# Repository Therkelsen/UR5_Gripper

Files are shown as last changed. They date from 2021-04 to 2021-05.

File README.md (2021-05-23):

# UR5_Gripper
dRobTek Group 6 - Second semester project for B.E. in Robotics Technology
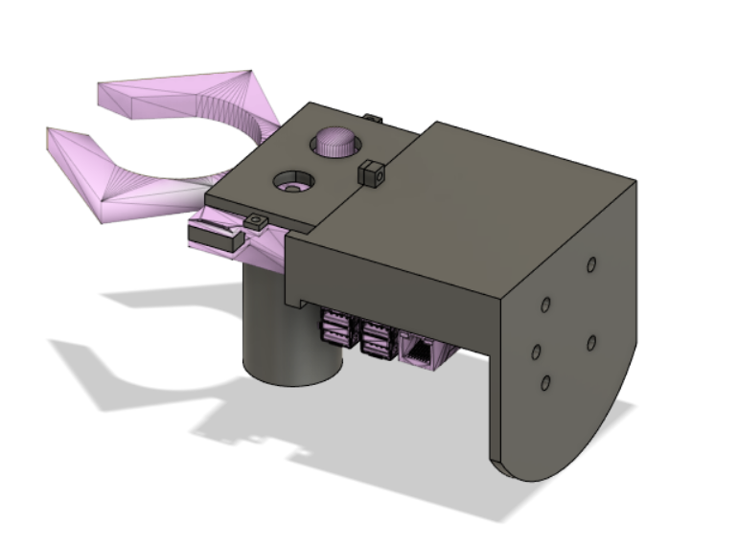
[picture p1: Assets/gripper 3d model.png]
UR5

<br>

## Problem
<div style="text-align: justify">A gripper for the Universal Robots UR5 robot is to be developed during this semester project. An idea could be to follow the block diagram below, but not required.</div>
<br>
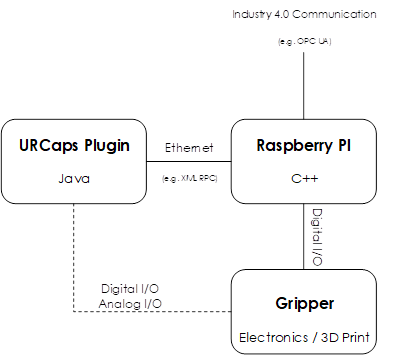
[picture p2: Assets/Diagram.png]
Diagram

<div style="text-align: justify">It is expected that you at least develop:<br>
•	A 3D model of a gripper that can be printed or otherwise constructed.<br>
•	Electronics to control the gripper.<br>
•	A URCaps plugin for the UR controller.<br>
•	Software design of a C++ Program developed on a Raspberry PI, a PC, or possibly both.<br>
•	A modern communication interface to the gripper (e.g. OPC UA). Ideas to an interface:<br>
•	The no. of grips<br>
•	Gripper force<br>
•	Gripper distance<br>
•	Etc.<br>
<br>
The gripper must fulfil the following requirements:<br>
•	Supply voltage: 24V (from external supply – you are not allowed to use the robot controller as power supply)<br>
•	The maximum gripper power use: 600mA<br>
•	It is not allowed to use the digital I/O from the UR robot. All I/O must be done through the Raspberry Pi microcontroller. Please remember that the power output from digital I/O is very limited.<br>
</div>
<br>

## Abstract
<div style="text-align: justify">
<a href="https://github.com/Therkelsen/UR5_Gripper/blob/main/Assets/Report.pdf">This report</a> presents the process of constructing and programming a gripper for the UR5-series industrial robotic arm, controlled through an XML-RPC-socket utilizing a URCap plugin on the robot. The gripper design is made for the purpose of hoisting a conventional 33 cl beverage can, which has the dimensions 122 mm in height and 65 mm in diameter. The final product is to be constructed with four main segments, firstly a URCap-plugin utilizing XML-RCP protocol to communicate with a Raspberry Pi. This single-board computer is connected to a motor, mounted to a 3D-printed gripper, which will open and close according to the XML-RPC-server method called by the URCap. Determinately, Industry 4.0 communication will run from the single-board computer to an external device, amassing and preserving information about the behaviour of the gripper.
<br>
First, the report introduces the different contents of the URCap-StarterPackage and the theoretical fundamentals of URCaps, following a walkthrough of the methods applied in building a URCap. This includes both an installation and program node fitting the criteria of the project. A more concrete view on how the individual Java-methods act together, to construct the interface and computer logics required in building a connection to an external device utilizing XML-RPC-protocol, is discussed. Furthermore, the structure of the C++-programmed XML-RPC-server will be covered, and additionally, how the different server method calls are utilized in another C++ program to instigate physical kineticism of the gripper. Thereafter, the designations and functionalities of the hardware components used will be listed and the process of modeling and printing the gripper, and the thoughts behind this design will be provided.
<br>
The proposed solution is presented in detail and discussed in terms of functionality in relation to the chosen scenario, and possible amendments, as well as thoughts on choices made throughout the process of effectuating a solution, will be shared. Lastly, the entire project will culminate in a summarized conclusion on the coalescence of URCaps, MotorControl, Industry 4.0 communication, and the 3D modeling and printing of the physical gripper - the four main segments embodying the objective of this project.
</div> 
<br>

## Introduction
<div style="text-align: justify">
The fourth industrial revolution as many in our time choose to call it, is constantly evolving, and evidently more of the industries as well as everyday processes, get automated. One of the many benefits of automation is, that the mistakes that humans make in the manual process are eliminated.
<br>
With this in mind, robots today are designed and constructed for all sorts of different purposes and in particular the 6-member robot arm has become an indispensable industrial tool, for example due to its universality.
This is not only due to the freedom of movement, but - as is the case for most robot arm manufacturers - also the freedom to switch between the robot arm tools. There are already a sea of tool manufacturers who invent everything between two- and three-finger grippers, vacuum grippers and grippers that utilize the so-called "soft robotics" technology. All these types of grippers, which can be used, for example, together with the robot arms from Universal Robots, which with their URCap software largely achieve the ambition of creating a universal robot arm.
<br>
The possibility of custom configuration through URCap allows for this project, where we have been given the task of designing and developing a gripper for a UR5 robot arm. This must be able to lift one or more objects of your choice. Here we have chosen to design a gripper that aims to lift a can, more specifically a standard 33 cl soda / beer can. The gripper itself is modeled in the CAD program Fusion 360, and is then physically made of 3D-printed plastic. The movements of the gripper are controlled by a DC motor, which is connected to a Raspberry Pi on which a motor driver is programmed using C++, to control the movement of the DC motor.
<br>
Furthermore, a URCap plugin has been developed in order to create a user-friendly interface. This URCap, consisting of a so-called Program Node and an Installation Node, establishes an XML-RPC connection to a server on the Raspberry Pi, thereby controlling the activation of the gripper's various functions.
</div>
<br>

## Conclusion
<div style="text-align: justify">
Through the work on the project, we have developed a well-functioning gripper in Fusion 360, with room in the gripper's cabinet for its electric components, for example the Raspberry Pi. 
<br>
The gripper is designed as consisting of two "fingers", designed to be able to carry an empty 33 cl soda / beer can. To control the gripper, a URCap, consisting of an installation and program node, has first been developed through Universal Robot's "URCap starter package". The installation node provides a UI for entering the port number and IP address, which is used to establish the XML-RPC connection. Through the program node, a UI has been programmed with a button for "grip" and "release", which call a method that makes an XML-RPC call to a C++ server that we have running on our Raspberry Pi. When this data is received, the C++ code executes the relevant method from the MotorControl class, depending on whether the URCap calls for a "grip" or "release", and here the gripper will do the physical action it is requested. 
<br>
We have tested the grip-release sequence and were able to successfully pick up a can and place it elsewhere. In addition, a TCP / IP connection has been created with the intention of Industry 4.0. Here, a comma-separated string is sent from the server, which tells the number of grips and the gripper's current state. Here, through a UI, the client side can monitor this data from an external device. Based on the problem formulation, it can finally be concluded that the project has largely been solved as intended, where one of the only shortcomings must be said to be a physical test of the gripper mounted on a UR5 robot arm.
</div>

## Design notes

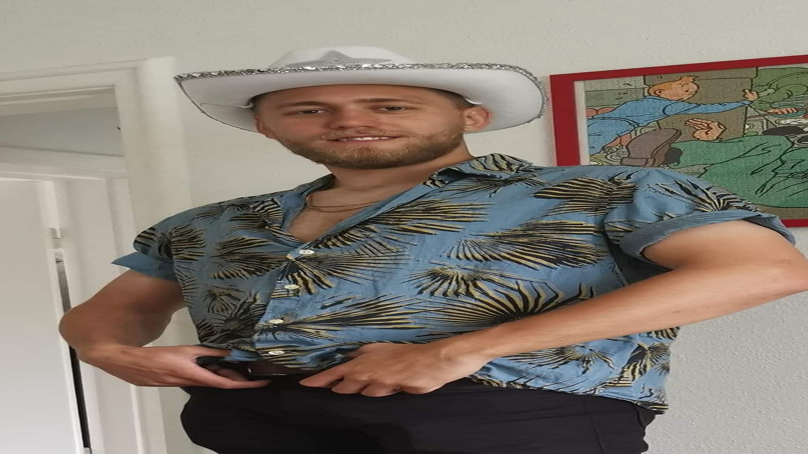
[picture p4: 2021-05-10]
Assets/august.png

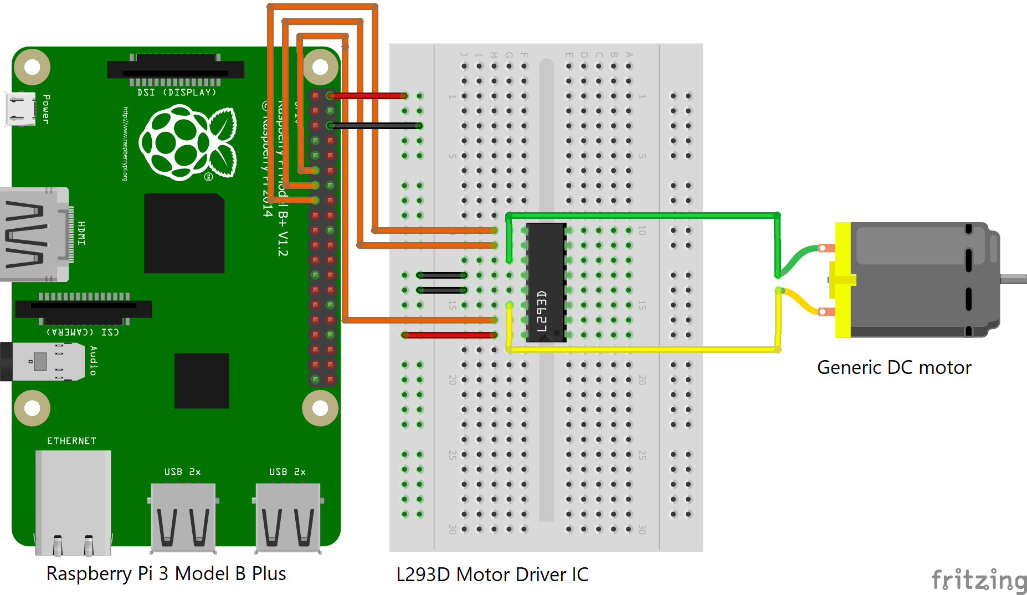
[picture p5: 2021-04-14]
Circuitry/L293D IC Diagram.png

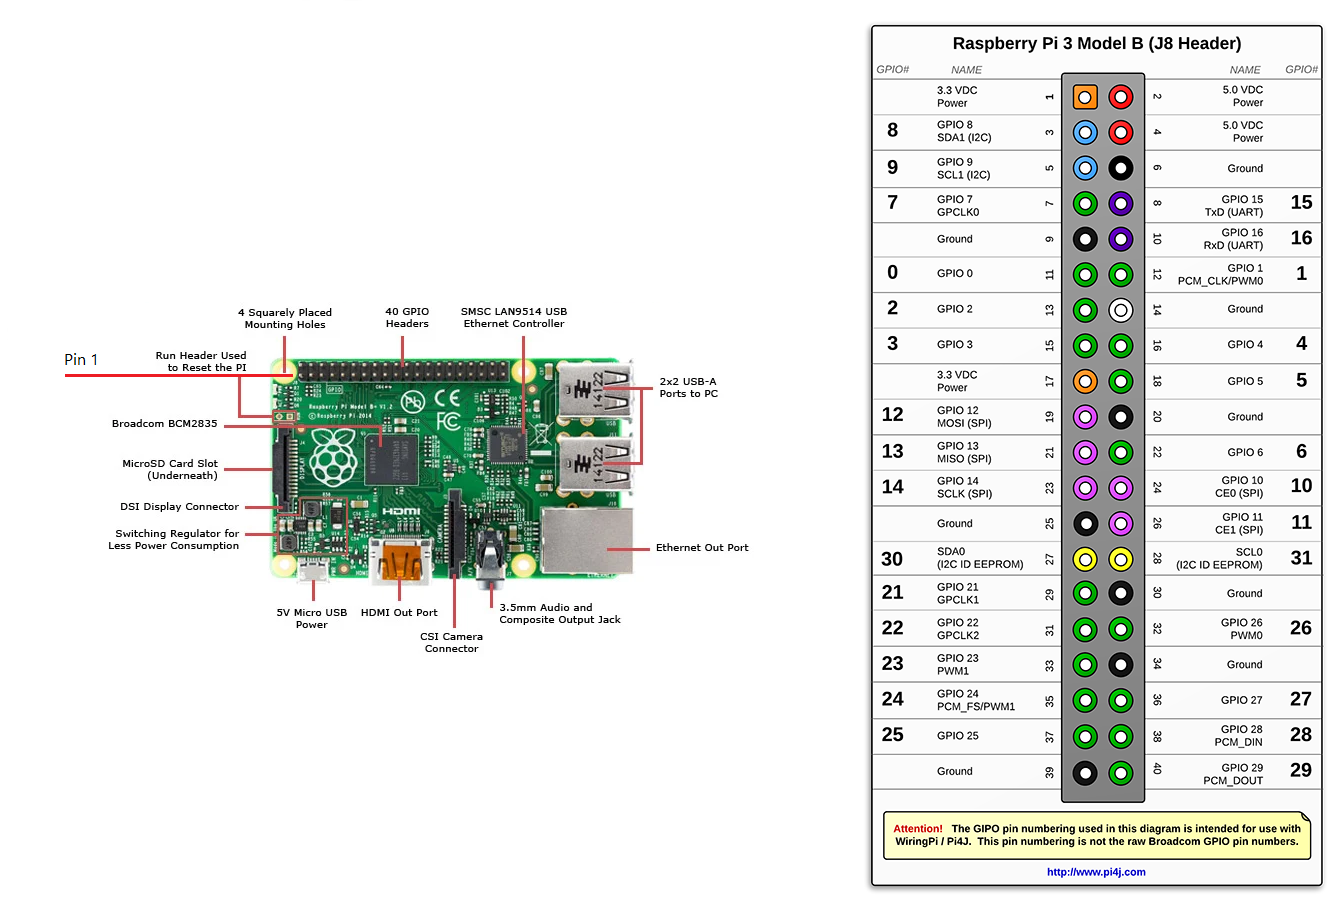
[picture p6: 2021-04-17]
Circuitry/Raspberry Pi 3 Model B Plus IO.png

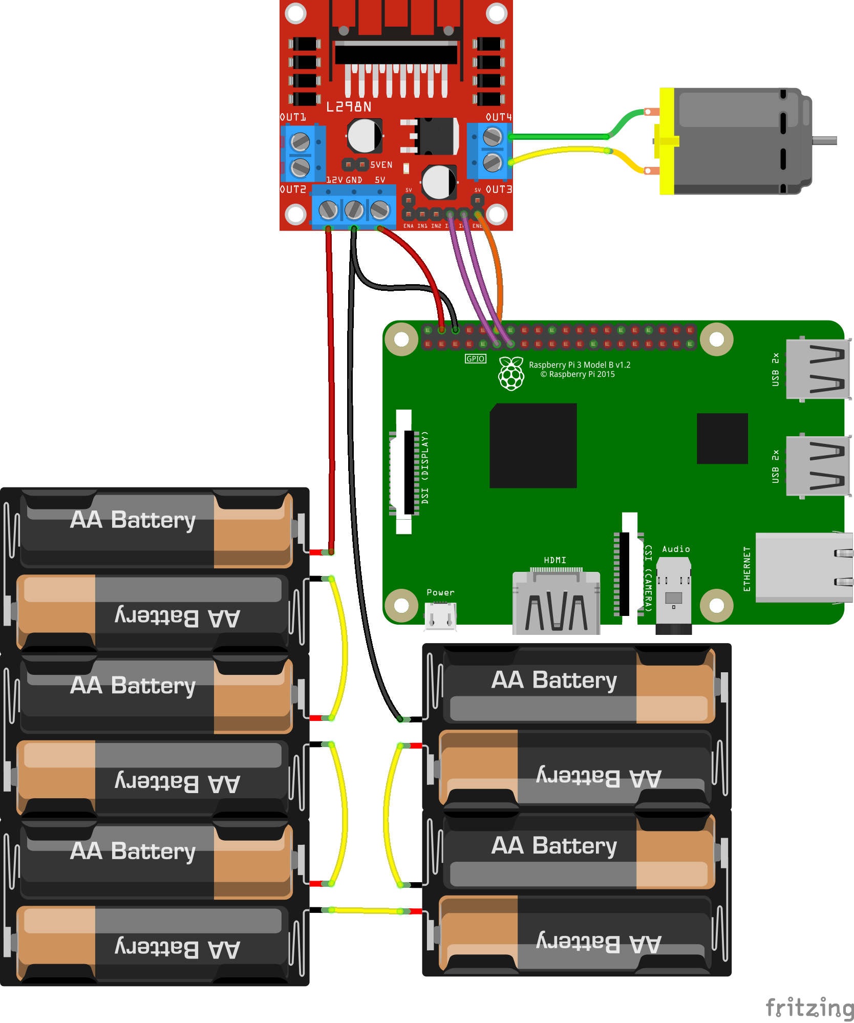
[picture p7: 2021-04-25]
Circuitry/L298N (Full Module) Diagram.png

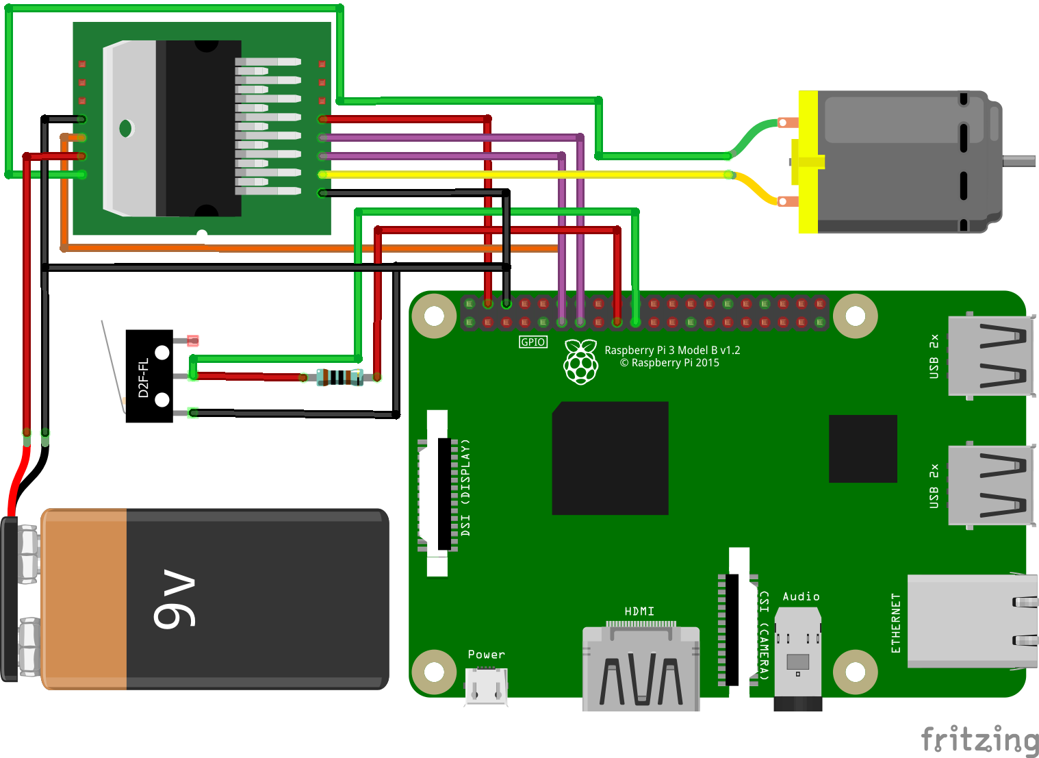
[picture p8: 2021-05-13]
Circuitry/Full Diagram.png

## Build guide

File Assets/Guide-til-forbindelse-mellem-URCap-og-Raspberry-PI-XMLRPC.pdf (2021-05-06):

## Guide til forbindelse mellem URCap og Raspberry PI (XMLRPC)

1. Få URSim og URCaps (sdk) op og køre
a. Nemmeste måde er at hente VirtualBox og installere URCaps starterpackage (https://plus.universal-robots.com/download-center/urcaps-starter-package/)
2. Lav en ny URCap
a. Vi gjorde det, at vi stjal eksempelkoden inde fra “~/sdk/sdk-1.11.0/samples/driver/gripper/com.ur.urcap.examples.driver.grip per.advancedgripper” (men der er flere eksempler man kan se på i samples og lære fra) og undersøgte hvilke funktioner der blev kaldt, når man kørte opengripper og releasegripper i URSim.
b. Når I har lavet noget URCap og vil have det ind i URSim skal I i terminalen, når I står i roden af jeres URCap mappe køre kommandoen “mvn install”.
c. I skal så i URSim installere den .urcap-fil, som bliver genereret og lagt ind i en mappe “target” og så genstarte URSim. (I kan med fordel have jeres URCap mappe placeret inde i den mappe, som URSim læser fra, når man tilføjer URCaps). For os var det “~/ursim/ursim-3.14.1.1031110/programs.UR5”
3. Hent og installer QT i Linux
a. Vi hentede deres installer fra deres hjemmeside.
b. Brug det link Preben havde sent på itslearning til at installere QT i starten af semesteret. Den registrerer selv, at det er på en linux maskine, man henter det på.
c. Når man skal køre installeren, skal man først lige give filen rettigheder til at køre. Dette gøres ved at åbne mappen, hvori filen ligger, og skrive “chmod +x *navn på fil*”. Herefter kan man blot skrive “./*navn på fil*” og installer vinduet kommer frem (minder meget om installeren af QT til windows).
d. Når I skal vælge parametrene vil der ikke være en MinGW mulighed, da det er noget man har lavet til windows for at simulere GCC compileren, som man bruger i Linux. I skal i stedet vælge den der hedder “Desktop gcc 64- bit” sammen med de andre ting, som skal vinges af (følg Prebens guide).
4. Installer XMLRPC (http://xmlrpc-c.sourceforge.net/downloading.php)
a. Vi installerede den “Stable” version under “Downloading From Subversion”.
b. I filen finder i en README.txt
i. Under afsnittet “PREREQUISITES” skal i enten hente W3C Libwww eller Curl (Vi hentede Curl)
ii. Følg derefter guiden under afsnittet “BUILDING, INSTALLING”
5. Brug af XMLRPC a. I .pro-filen i jeres QMake projekt (QT Creator) indsætter i følgende kode (credits til Peter Olsen):

i.

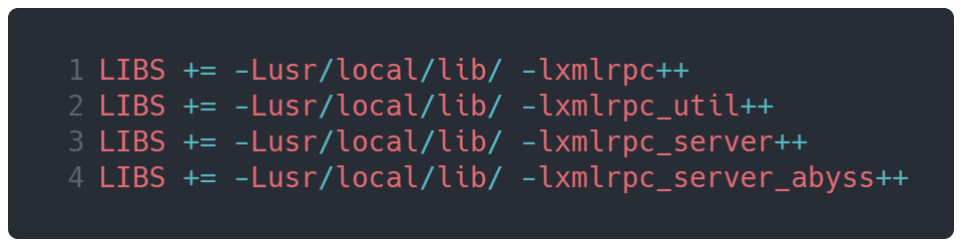
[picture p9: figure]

b. I Teams har Peter Olsen lagt en optagelse af noget af sit XMLRPC setup, som er hvad vi brugte til at få det sidste til at give mening. Det indeholder lidt af, hvordan man skriver det i sit URCaps, hvordan URCaps fungerer samt hvordan man skriver sin CPP kode (XMLRPC server), så den kan modtage informationerne fra URCaps.

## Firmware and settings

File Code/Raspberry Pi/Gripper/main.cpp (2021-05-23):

#include "motorcontrol.h"
#include "xmlrpc.h"
#include <iostream>
#include <wiringPi.h>
#include <softPwm.h>
#include "tcp_server.h"

#define motorEnable 1
#define motorPin1 0
#define motorPin2 2
#define sensor 12
#define xmlrpcPort 12345
#define tcpipPort 8080

using namespace std;

int main() {
    softPwmStop(motorEnable);
    softPwmWrite(motorEnable, 0);

    tcp_server socket(8080);

    MotorControl mc(motorEnable, motorPin1, motorPin2, sensor, socket);

    mc.calibrate();

    softPwmWrite(motorEnable, 0);

    XMLRPC server(mc);
    server.runServer(xmlrpcPort);

    return 0;
}

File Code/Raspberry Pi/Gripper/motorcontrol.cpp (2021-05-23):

#include "motorcontrol.h"
#include "tcp_server.h"
#include <wiringPi.h>
#include <softPwm.h>
#include <iostream>
#include <sstream>

MotorControl::MotorControl(){};

MotorControl::MotorControl(int motorEnable, int motorPin1, int motorPin2, int sensor, tcp_server socket) {
    _motorEnable = motorEnable;
    _motorPin1 = motorPin1;
    _motorPin2 = motorPin2;
    _sensor = sensor;

    _numberOfGrips = 0;
    STATE = "SETUP";

    this->socket = socket;

    wiringPiSetup();

    std::cout << "MotorControl: Inclusions and definitions handled" << std::endl;

    pinMode(_motorEnable,OUTPUT);
    pinMode(_motorPin1,OUTPUT);
    pinMode(_motorPin2,OUTPUT);
    pinMode(_sensor, INPUT);

    softPwmCreate(_motorEnable,35,100);

    std::cout << "MotorControl: GPIO access has been set up" << std::endl;

    std::stringstream ss;
    ss << _numberOfGrips;
    ss >> string;
    string.append(", ");
    string.append(STATE);

    socket.runServer(string);
}

int MotorControl::calibrate(){
    std::cout << "MotorControl: Calibrating gripper" << std::endl;
    STATE = " CALIBRATE";
    while (true) {
        if (digitalRead(_sensor) == HIGH) {
            digitalWrite(_motorPin1, HIGH);
            digitalWrite(_motorPin2, LOW);
            softPwmWrite(_motorEnable, 100);
        } else {
            softPwmWrite(_motorEnable,0);
            digitalWrite(_motorPin1, LOW);
            digitalWrite(_motorPin2, HIGH);

            //sendString();
            return 0;
        }
    }
}

void MotorControl::grip(unsigned int time){
    std::cout << "MotorControl: Gripping object" << std::endl;

    //  Calibrate gripper
    calibrate();

    STATE = "GRIP";
    _numberOfGrips++;

    //  Run motor for x seconds, to grip can
    softPwmWrite(_motorEnable,100);
    delay(time);
    softPwmWrite(_motorEnable,0);
    sendString();
}

void MotorControl::release(){
    //  Just calls calibrate, is called release for semantic reasons
    calibrate();
}

void MotorControl::close(unsigned int time) {
    std::cout << "MotorControl: Closing gripper" << std::endl;
    softPwmWrite(_motorEnable,100);
    delay(time);
    softPwmWrite(_motorEnable,0);
    STATE = "CLOSE";
    sendString();
}

void MotorControl::sendString() {
    std::cout << "MotorControl: Sending status string" << std::endl;
    std::stringstream ss;
    ss << _numberOfGrips;
    ss >> string;
    string.append(", ");
    string.append(STATE);

    std::cout << "String: " << string << std::endl;

    socket.runServer(string);
}

void MotorControl::reverse(unsigned int time){
    digitalWrite(_motorPin1, HIGH);
    digitalWrite(_motorPin2, LOW);
    softPwmWrite(_motorEnable,100);
    delay(time);
    digitalWrite(_motorPin1, LOW);
    digitalWrite(_motorPin2, HIGH);
    softPwmWrite(_motorEnable,0);
}

void MotorControl::test(){
    while (true) {
        if (digitalRead(_sensor) != HIGH) {
            std::cout << "HIGH" << std::endl;
        } else {
            std::cout << "LOW" << std::endl;
        }
    }
}

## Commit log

2021-04-14 Drew an initial wiring diagram
    [Initial diagram.fzz]
2021-04-17 Create Raspberry Pi 3 Model B Plus IO.png
2021-04-17 Updated I/O diagram, uploaded some Arduino test come
2021-04-17 Uploading LED test code from qt on raspberry pi
2021-04-25 Updated wiring diagram with correct ras pi model
    [L298N Diagram.fzz]
2021-04-25 Recreated wiring diagram with just IC, as well
    [L298N (Full Module) Diagram.fzz, L298N (Only IC) Diagram.fzz, L298N Diagram.fzz]
2021-04-27 Wrote some basic boilerplate code for motor control - Will probably be replaced soon
    [main.cpp]
2021-05-01 Fixed crocodile brackets turning the wrong way
    [main.cpp]
2021-05-05 Added some test code for motor control, which works.
2021-05-05 Refactoring code to put motor control in its own class, so code looks more clean.
2021-05-13 Fixed IC wiring, added full wiring diagram including the microswitch and changed batteries to only be 9V.
    [Full Diagram.fzz, L298N (Only IC) Diagram.fzz]
2021-05-19 XMLRPC as a class
    [Full Diagram.fzz]
2021-05-19 Revert "XMLRPC as a class"
    This reverts commit 2b1ceb4012de03a1daa7d3698eebdc75883163b2.
    [Full Diagram.fzz]
2021-05-23 Added working TCP/IP socket/client connection to comply with Industry 4.0 target.
2021-05-23 Create gripper 3d model.png
